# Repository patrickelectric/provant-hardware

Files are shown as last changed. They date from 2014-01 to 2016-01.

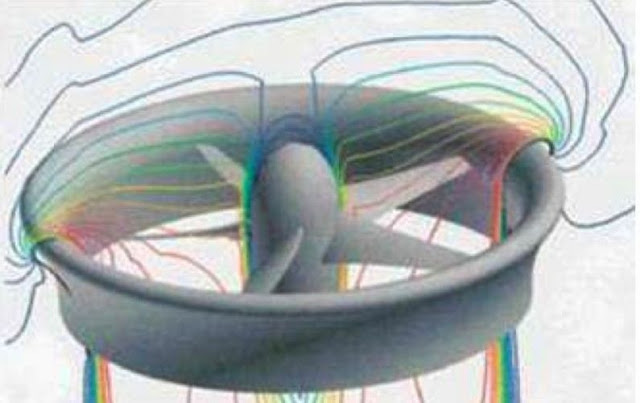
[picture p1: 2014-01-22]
mechanics/images/smCFDAeroAnal.jpg

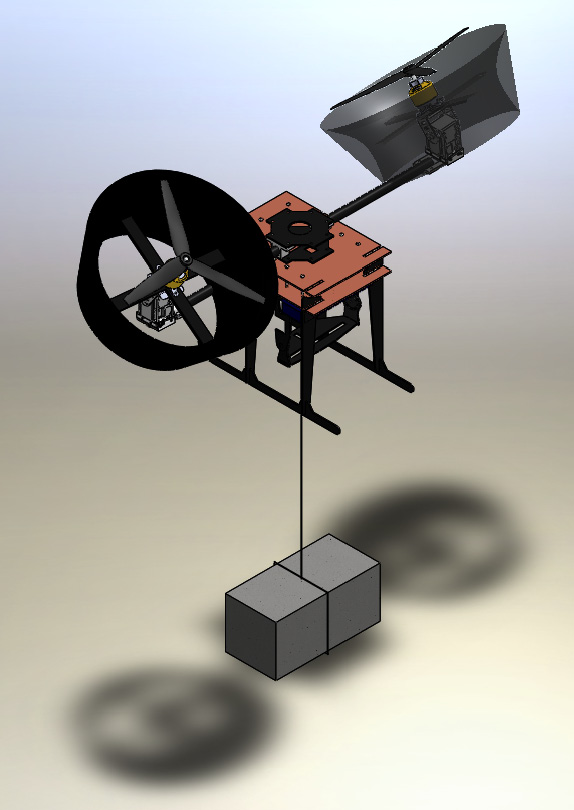
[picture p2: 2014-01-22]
mechanics/images/montagem_completa_tijolo_rodrigo.jpg

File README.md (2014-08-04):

provant-hardware
================

#### Descrição ####

Repositório para projeto de Hardware (mecânica e eletrônica) do proVANT. 

#### Estrutura do repositório ####

A pasta _mechanics_ está estruturada em três subpastas:

- __drawings__ : Desenhos técnicos das partes modeladas.
- __images__ :  Renderizações e _prints_ de modelos completos e peças. 
- __models__ : Arquivos dos modelos 3D de partes e montagens.

Os modelos 3D foram desenvolvidos em sua maioria com o uso do CAD [_Solid Works_](www.solidworks.com).

Os esquemáticos e layouts das placas deste projeto foram desenvolvidas com software de EDA [_Eagle_](www.cadsoftusa.com/), e estão contidos na pasta _electronics_. Esta está estruturada em:

- __lib__ :  Contem bibliotecas de componentes exclusivos do projeto, bem como bibliotecas de terceiros (não padrões no Eagle) que foram utilizadas.
- __stm32-e407-shield__ : Contem esquemático/layout do shield desenvolvido para a placa __antiga__ utilizada no projeto, a [STM32-H407](https://www.olimex.com/Products/ARM/ST/STM32-H407/open-source-hardware). Esta pasta e seus conteúdos podem ser considerados __obsoletos__ .
- __stm32f4discovery-shield__ : Contem o esquemático/layout da placa breakout sendo utilizada atualmente no projeto, projetada para a [STM32F4-Discovery](http://www.st.com/web/catalog/tools/FM116/SC959/SS1532/PF252419?sc=internet/evalboard/product/252419.jsp).

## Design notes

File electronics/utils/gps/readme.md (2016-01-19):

Manual de montagem dos perifericos do GPS
====================================

Todos os esquematicos nesta pasta foram realizados utilizando o Eagle, boa parte das bibliotecas utilizadas foram extraidas da [bilbioteca da SparkFun](https://github.com/sparkfun/SparkFun-Eagle-Libraries). 

##### Instalacao de bilbiotecas para o Eagle

O procedimento de instalacao das bibliotecas para o Eagle consta [neste link](
https://learn.sparkfun.com/tutorials/how-to-install-and-setup-eagle/using-the-sparkfun-libraries).

##### Connector_cable
Nesta pasta se encontra o conector utilizado para ter acesso aos pinos para leitura de dados basicos do GPS OEMStar, sendo eles: RX,TX,VCC,GND.

##### Connector_protoboard
Nesta pasta se encontra o conector utilizado para adaptar o conector do GPS OEMStar a protoboard.

##### Arduino_mini

Esta pasta em questao consta o conversor das mensagens do GPS para o VANT.
As mensagens que sao enviadas em formato de String sao de dificil tratamento utilizando as bibliotecas basicas do ARM que estao sendo atualmente utizadas no projeto.
Podendo variar o tamanho, formato e tipo.
As informacoes sobre as mensagens e o GPS podem ser encontradas [aqui](http://www.novatel.com/assets/Documents/Bulletins/apn026.pdf).

Alguns exemplos de mensagens recebidas:
```
#BESTPOSA,COM1,0,93.0,UNKNOWN,0,90.000,004c0000,7145,12014;INSUFFICIENT_OBS,NONE,0.00000000000,0.00000000000,0.0000,0.0000,WGS84,0.0000,0.0000,0.0000,"",0.000,0.000,0,0,0,0,0,00,00,00*18de8d75
#BESTPOSA,COM1,0,91.5,COARSESTEERING,1847,221137.000,004c0000,7145,12014;INSUFFICIENT_OBS,NONE,0.00000000000,0.00000000000,0.0000,0.0000,WGS84,0.0000,0.0000,0.0000,"",0.000,0.000,0,0,0,0,0,00,00,00*43baf10b
#BESTPOSA,COM1,0,87.0,FINESTEERING,1847,221347.000,00440000,7145,12014;SOL_COMPUTED,SINGLE,-27.60022826035,-48.51710556420,-2.9004,0.4000,WGS84,22.9611,14.4112,31.3712,"",0.000,0.000,4,4,4,4,0
```

#### Sobre o GPS
Boa parte da documentacao do GPS OEMStar pode ser encontrado dentro do Dropbox do projeto.
> proVANT/birotor/components/electronics/datasheets/sensors/GPS/novatek_oemstar

As bibliotecas para realizar a comunicação do GPS com o VANT esta localizado em:
> provant-software/io-board/stm32f4/base/modules/io/c_io_novatel.c/h

##### Iniciando comunicacao
Primeiramente deve ser feito um dos conectores, podendo ser tanto o connector_protoboard quanto o connector_cable, pois ambos dao acesso aos pinos basicos ditos anteriormente.

Os pinos que deveram ser conectados sao: 1,2 como VCC; 10,13,16,18 como GND; 11 como TX; 12 como RX;

| Signal | Behavior | Descriptions | Pin |
|---|---|---|-----|
| LNA_PWR  | Input DC | Power supply for external antenna | 1 |
| Vin | Input DC | DC power supply for card | 2 |
| USB d- | Bi-derectional | USB interface data - | 3 |
| USB d+ | Bi-directional | USB interface data + | 4 |
| RESETIN  | See strobes | Card reset | 5 |
| VARF | output | VARF | 6 |
| Reserved | | | |
| Reserved | | | |
| Event1 | Input | Strobe, see strobes, default: Event1 | 9 |
| GND | Ground | Digita Ground | 10  |
| COM1_Tx  | Output | Transmitted Data for COM 1 output | 11  |
| COM1_Rx  | Input | Receved Data for COM 1 input | 12  |
| GND | Ground | Digital Ground | 13  |
| COM2_Tx  | Output | Transmitted Data for COM 2 output | 14  |
| COM2_Rx  | Input | Received Data for COM 2 input | 15  |
| GND | Ground | Digital Ground | 16  |
| PV | Output | Output indicates 'good solution' or vallid FPS position when high | 17  |
| GND | Ground | Digital Gorund | 18  |
| PPS | See strobes | Pulse output synchronized to GPS Time | 19  |
| | | | |

Com estes pinos conectados em seus respectivos lugares, pode ser realizado os testes.

###### Software
Com os pinos conectados em um microcontrolador ou numa interface USB-serial, pode-se iniciar a comunicacao, com o baudrate de 9600, pedindo ao dispostivo a melhor posicao utilizando o comando:
```
LOG COM1 BESTPOSA ONTIME 1
```
Enquanto o GPS nao detectar a posicao, ele retornada a msg:
```
#BESTPOSA,COM1,0,93.0,UNKNOWN,0,90.000,004c0000,7145,12014;INSUFFICIENT_OBS,NONE,0.00000000000,0.00000000000,0.0000,0.0000,WGS84,0.0000,0.0000,0.0000,"",0.000,0.000,0,0,0,0,0,00,00,00*18de8d75
```

Um exemplo de codigo para ter uma comunicacao do GPS pode ser encontrado abaixo, este mesmo codigo pode ser utilizado para realizar a comunicacao do GPS com o VANT.
Este codigo foi utilizado para a placa arduino_mini, utilizando os pinos 10 e 11 para a comunicacao serial via software.

```
// all the information about the data can be obtained from: http://www.novatel.com/assets/Documents/Bulletins/apn026.pdf
// or on Dropbox: Geodetic Principles.pdf

// to start, send the command:
// log com1 bestposa ontime 1

#include <SoftwareSerial.h>

char * floatToString(char * outstr, float value, int places);

const int led = 13;
String started="[COM1]";
String bestposa="#BESTPOSA";
String unknown="UNKNOWN";
String coarsesteering="COARSESTEERING";
String finesteering="FINESTEERING";
String insufficient_obs="INSUFFICIENT_OBS";
String sol_computed="SOL_COMPUTED";

#define PROCESS_BESTPOSA      1
#define PROCESS_BESTPOSA_DATA 1
#define DEBUG                 1

//char  float_pos1[]={2,3}
//float Buffer[32]
bool SOL_COMPUTED_FLAG=0;
SoftwareSerial SoSerial(10, 11); // TX = digital pin 10, RX = digital pin 11

void setup() 
{
  delay(2000);
  // initialize serial:
  Serial.begin(9600);
  SoSerial.begin(9600);
  // make the pins outputs:
  pinMode(led, OUTPUT); 
}

void loop() 
{
  digitalWrite(led,HIGH);
  // if there's any serial available, read it:
  while (SoSerial.available() > 0)
  {
    digitalWrite(led,LOW);      // show that we received something
    char newlinearray[300]={};
    SoSerial.readBytesUntil('\n',newlinearray,300);
    String newline = newlinearray;
    
    if(DEBUG)
    {
      Serial.print("[R] >");
      Serial.print(newline);
      Serial.println("<");    // show what received
    }

    if(PROCESS_BESTPOSA && newline.length()>10)
    {
      // process bestposa
      int beginIdx = 0;
      int endIdx = newline.indexOf(";")-6;      // the last ',' of bestposa is ';' -6 char 
      int idx = newline.indexOf(",",beginIdx);  // take the first ','
      String arg[50];
      for(int i=0;i<50 && idx!=endIdx;i++)      // take all data
      {
        arg[i] = newline.substring(beginIdx, idx);
        beginIdx = idx + 1;
        idx = newline.indexOf(",", beginIdx);
        if(DEBUG)
        {
          Serial.print(i);
          Serial.print(" >");
          Serial.println(arg[i]);
        }
      }
    }

    if(DEBUG)
      Serial.println("###################");

    if(PROCESS_BESTPOSA_DATA && newline.length()>10)
    {
      // process data
      SOL_COMPUTED_FLAG = false;
      
      int beginIdx = newline.indexOf(";")+1;
      int endIdx = -1;
      int idx = newline.indexOf(",",beginIdx);
      String arg[50];
      
      for(int i=0;i<50 && idx!=endIdx;i++)
      {
        arg[i] = newline.substring(beginIdx, idx);
        beginIdx = idx + 1;
        idx = newline.indexOf(",", beginIdx);
        if(DEBUG)
        {
          Serial.print(i);
          Serial.print(" > ");
          Serial.println(arg[i]);
        }
      }
      if(arg[0] == sol_computed)
        SOL_COMPUTED_FLAG = true;

        if(SOL_COMPUTED_FLAG)
        {
          Serial.print("R");
          Serial.write(arg[2].length());
          Serial.write(arg[3].length());
          float heigh = arg[5].toFloat()+arg[4].toFloat();
          char buffer[25];
          String Heigh = floatToString(buffer, heigh, 5);
          Serial.write(Heigh.length());
          
          Serial.print(arg[2]);
          Serial.print(",");
          Serial.print(arg[3]);
          Serial.print(",");
          Serial.print(Heigh);
          
          Serial.print('\n');
        }
        else
        {
          Serial.print("R");
          Serial.write(13);
          Serial.write(13);
          Serial.write(7);
          Serial.print("0.00000000000");
          Serial.print(",");
          Serial.print("0.00000000000");
          Serial.print(",");
          Serial.print("0.00000");
          Serial.print('\n');
        }
    }   
    
  } // while serial avaiable

  // send data VANT->GPS
  while(Serial.available()>0)
  {
      SoSerial.write(Serial.read());
  }
      
}

char * floatToString(char * outstr, float value, int places)
{
   int minwidth=0;bool rightjustify=false;
    // this is used to write a float value to string, outstr.  oustr is also the return value.
    int digit;
    float tens = 0.1;
    int tenscount = 0;
    int i;
    float tempfloat = value;
    int c = 0;
    int charcount = 1;
    int extra = 0;
    // make sure we round properly. this could use pow from <math.h>, but doesn't seem worth the import
    // if this rounding step isn't here, the value  54.321 prints as 54.3209

    // calculate rounding term d:   0.5/pow(10,places)  
    float d = 0.5;
    if (value < 0)
        d *= -1.0;
    // divide by ten for each decimal place
    for (i = 0; i < places; i++)
        d/= 10.0;    
    // this small addition, combined with truncation will round our values properly 
    tempfloat +=  d;

    // first get value tens to be the large power of ten less than value    
    if (value < 0)
        tempfloat *= -1.0;
    while ((tens * 10.0) <= tempfloat) {
        tens *= 10.0;
        tenscount += 1;
    }

    if (tenscount > 0)
        charcount += tenscount;
    else
        charcount += 1;

    if (value < 0)
        charcount += 1;
    charcount += 1 + places;

    minwidth += 1; // both count the null final character
    if (minwidth > charcount){        
        extra = minwidth - charcount;
        charcount = minwidth;
    }

    if (extra > 0 and rightjustify) {
        for (int i = 0; i< extra; i++) {
            outstr[c++] = ' ';
        }
    }

    // write out the negative if needed
    if (value < 0)
        outstr[c++] = '-';

    if (tenscount == 0) 
        outstr[c++] = '0';

    for (i=0; i< tenscount; i++) {
        digit = (int) (tempfloat/tens);
        itoa(digit, &outstr[c++], 10);
        tempfloat = tempfloat - ((float)digit * tens);
        tens /= 10.0;
    }

    // if no places after decimal, stop now and return

    // otherwise, write the point and continue on
    if (places > 0)
    outstr[c++] = '.';

    // now write out each decimal place by shifting digits one by one into the ones place and writing the truncated value
    for (i = 0; i < places; i++) {
        tempfloat *= 10.0; 
        digit = (int) tempfloat;
        itoa(digit, &outstr[c++], 10);
        // once written, subtract off that digit
        tempfloat = tempfloat - (float) digit; 
    }
    if (extra > 0 and not rightjustify) {
        for (int i = 0; i< extra; i++) {
            outstr[c++] = ' ';
        }
    }

    outstr[c++] = '\0';
    return outstr;
}
```

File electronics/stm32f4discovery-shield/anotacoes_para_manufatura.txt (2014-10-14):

Anotações para schematic-for-manuf.brd
======================================

Tamanho de furações (mínimo do fabricante = 0.4mm)
+ Para conectores RJ11 - pads = 0.7mm [0,027559 polegadas]
+ Para conectores RJ11 - dois conectores mecânicos laterais = 2.0mm [0,078740 polegadas]
+ Para DIP (todas as barras de pino e de soquete) = 0.9mm [0,035433 polegadas]

Larguras de trilhas (mínimo do fabricante = 8mils)
+ Para malhas de sinais = 12 mil 
	(para passar trilhas entre pads é adequado. O espaço entre pads é de ~34mils; sobram ~11 mils pra cada lado, o que fica ok com o mínimo de espaçamento de 8mils do fabricante)
+ Para as malhas de alimentação = 24 mil (Linhas de 5V, 3V3 e GND se necessário). rip
+ para uma malha de alimentação, quando ela estiver conectando o último elemento de uma linha = 16mil

Tamanho dos pads: 
+ Pads e vias serao octogonais com 66mil de diametro. 

Diferenças principais entre a placa para fresagem e para manufatura
===================================================================

+ Parte-se do pressuposto de furos metalizados, que conectam o pad no TOP e no BOTTOM.
+ Utilizam-se trilhas partindo dos pads do TOP dos conectores RJ12 e no soquete da Discovery (barra-pino).
+ A tolerância apresentada na seção anterior permite o uso de trilhas passando por entre pads.

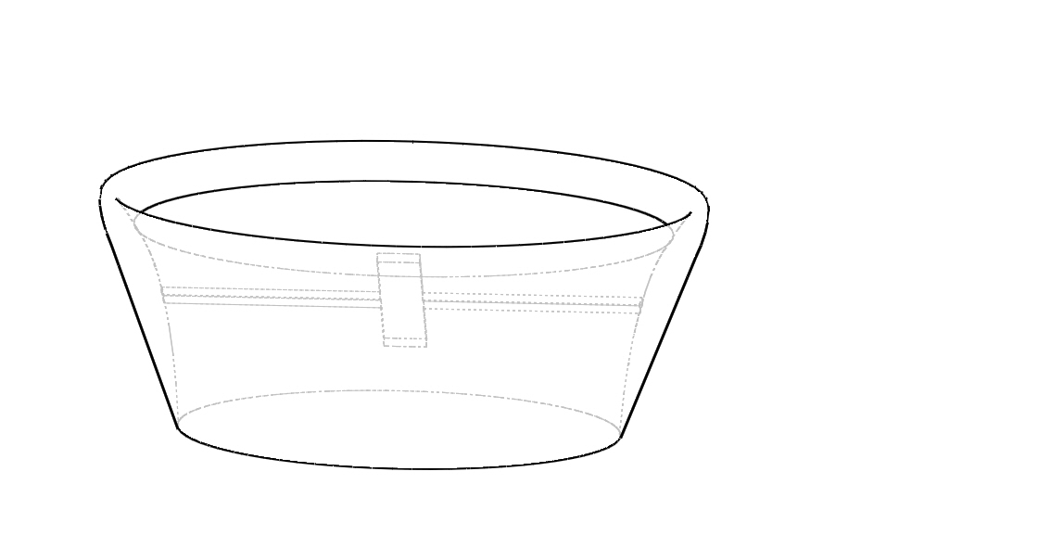
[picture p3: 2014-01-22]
mechanics/images/ducted fan_novo.JPG

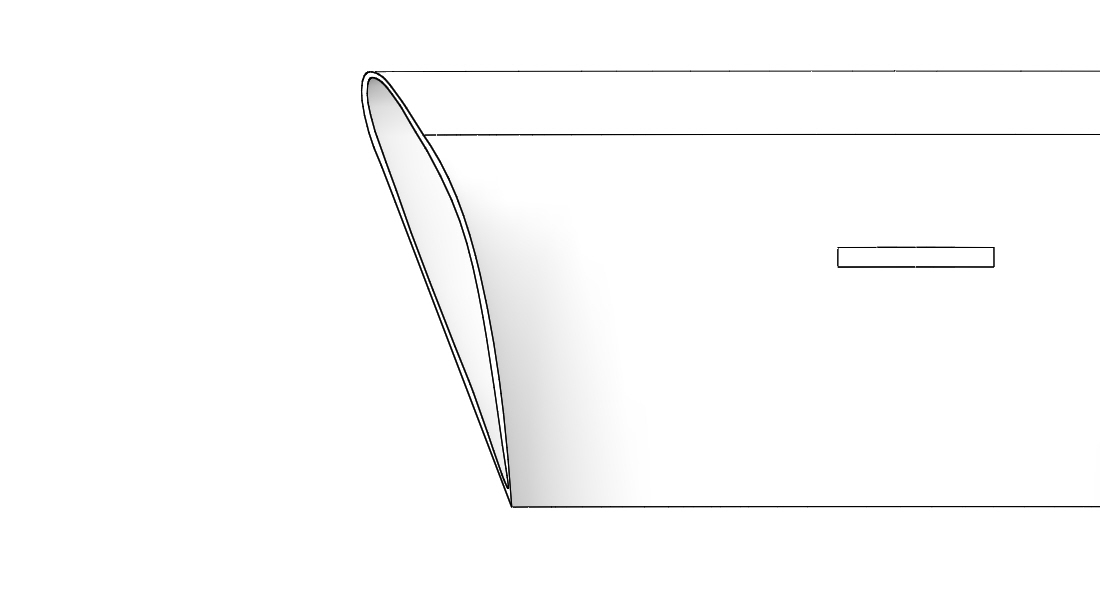
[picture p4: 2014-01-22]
mechanics/images/ducted fan_novo_corte.JPG

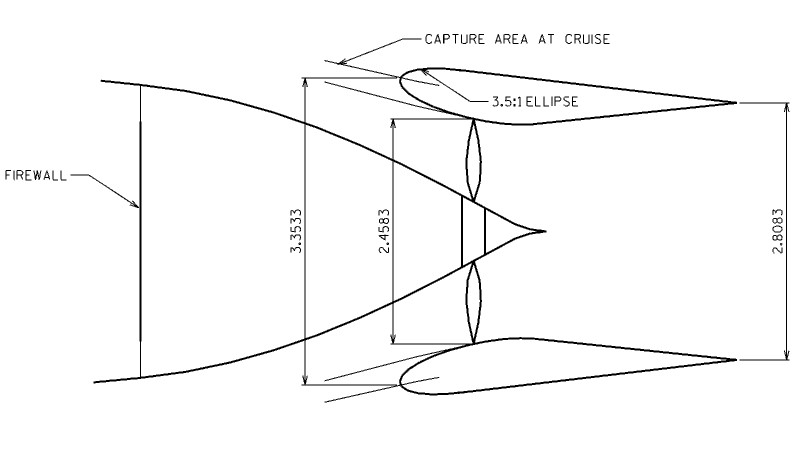
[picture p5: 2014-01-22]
mechanics/images/fanlayout.jpg

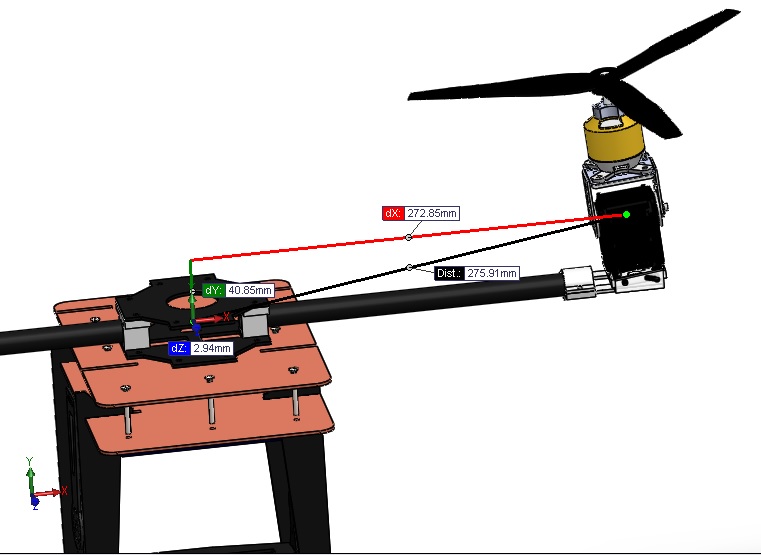
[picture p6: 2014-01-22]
mechanics/images/distancias_centro.jpg

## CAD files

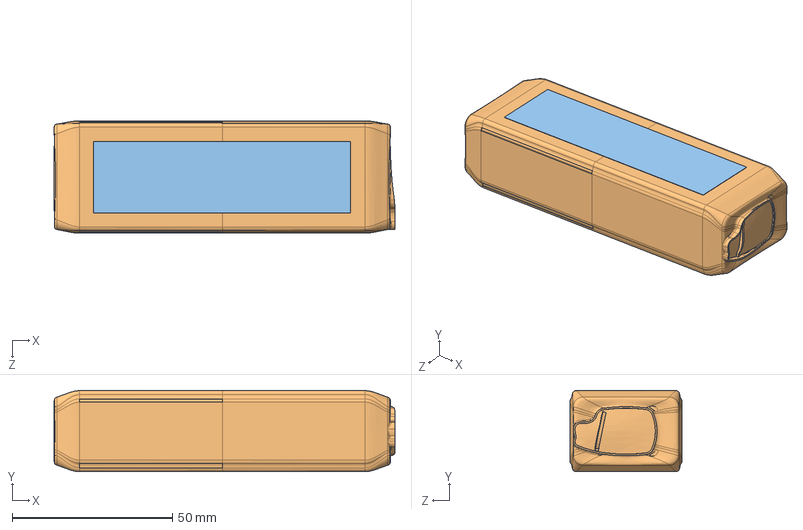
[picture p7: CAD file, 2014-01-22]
mechanics/models/Bateria/LiPo_1.SLDASM
106.3 x 25.4 x 35.0 mm
Inner end
Casing
Label

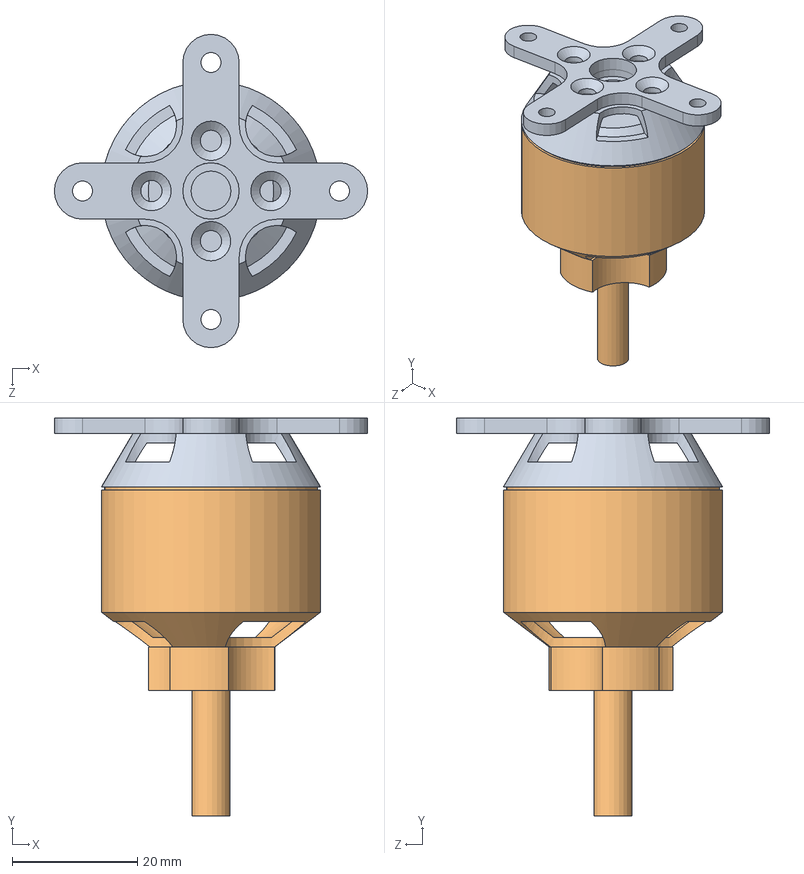
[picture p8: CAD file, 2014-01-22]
mechanics/models/MotorBrushless/MotorBrushless.SLDASM
50.0 x 63.5 x 50.0 mm
AXI2814-20-base
AXI2814-20-rotor^MotorBrushless

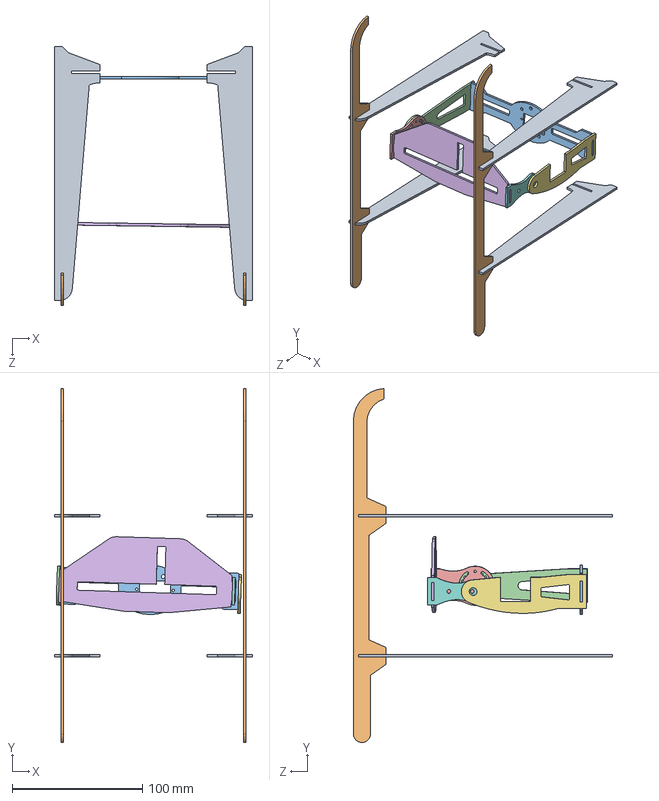
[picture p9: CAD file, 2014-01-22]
mechanics/models/trem_pouso_montagem.SLDASM
152.0 x 271.5 x 198.9 mm
tremdepouso_perna x 4
tremdepouso_sky x 2
Peça2
Peça5
Peça4
Peça3
Peça8-suporte_camera
Peça7-suporte_camera

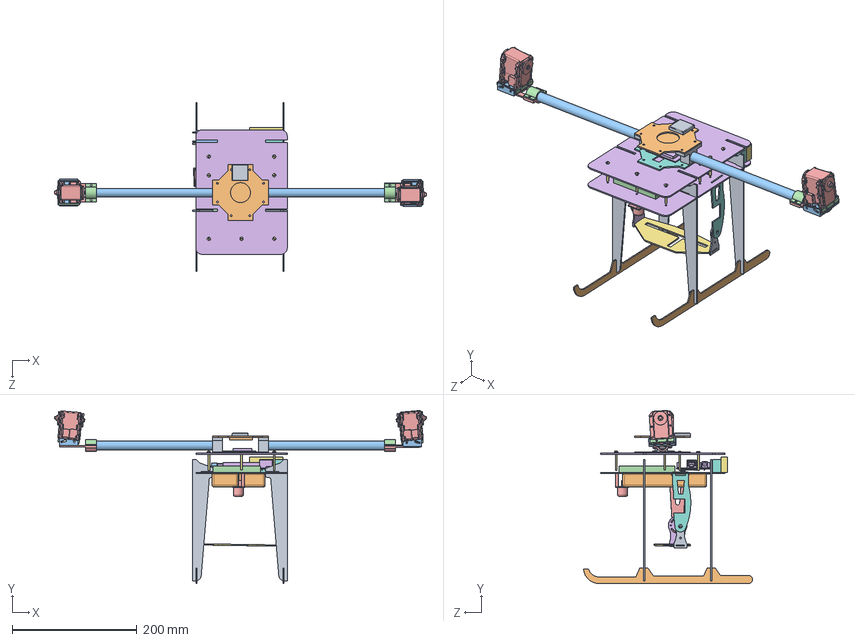
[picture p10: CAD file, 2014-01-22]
mechanics/models/montagem_inferior_eletronica.SLDASM
597.6 x 278.1 x 271.5 mm
tremdepouso_perna x 4
tremdepouso_sky x 2
Peça1
Peça2
Peça5
Peça4
Peça3
Peça8-suporte_camera
Peça7-suporte_camera
bateria1 x 2
suporte_inclinado_base x 2
suporte_inclinado_haste x 2
servo_rx24F x 2
chapa x 2
countersunk slotted raised head screw_iso x 9
centro_helice_2
suporte_haste x 2
centro_helice_1
helice_haste x 2
suporte_helice_2 x 2
suporte_helice x 2
Beagle
5v5a_converter
9v_45a_converter
gps_antenna
gps_base
rx
cortex m4
sonar
imu

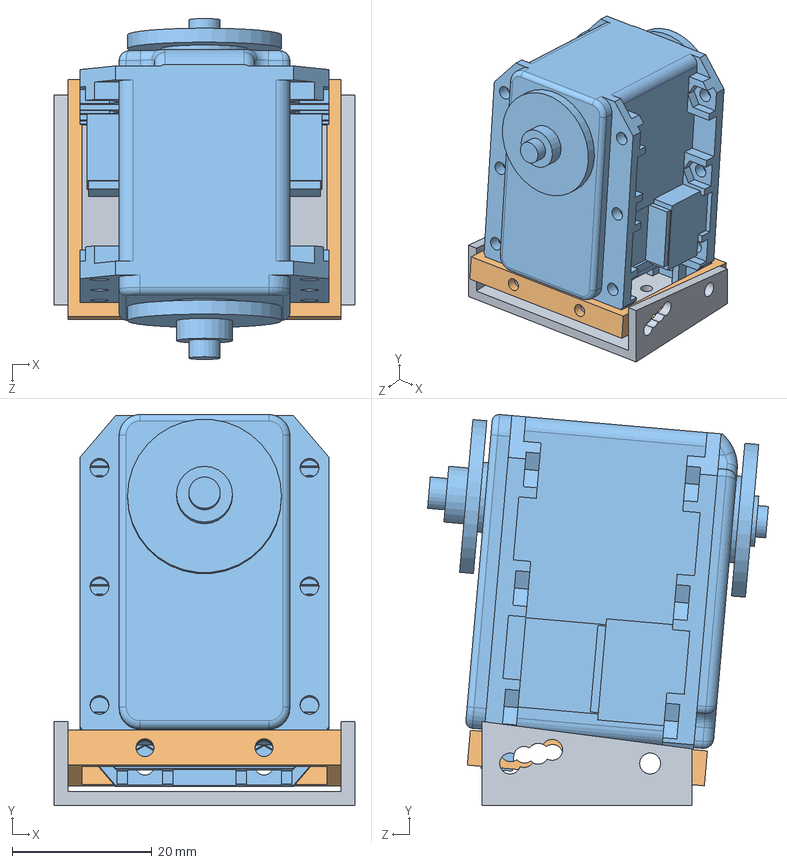
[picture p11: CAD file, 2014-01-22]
mechanics/models/suporte_inclinado_montagem_2.SLDASM
43.0 x 55.9 x 48.7 mm
suporte_inclinado_base
suporte_inclinado_haste
servo_rx24F

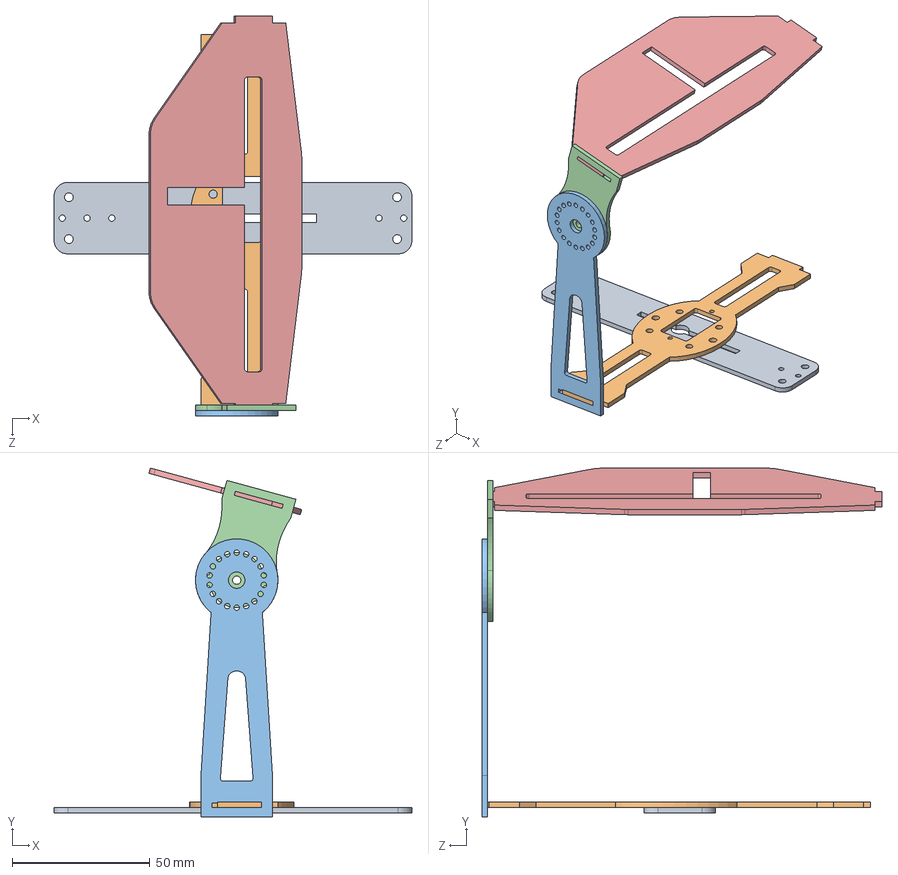
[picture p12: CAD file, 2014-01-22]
mechanics/models/suporte_camera.SLDASM
130.0 x 126.7 x 145.1 mm
Peça1
Peça2
Peça5
Peça4
Peça3

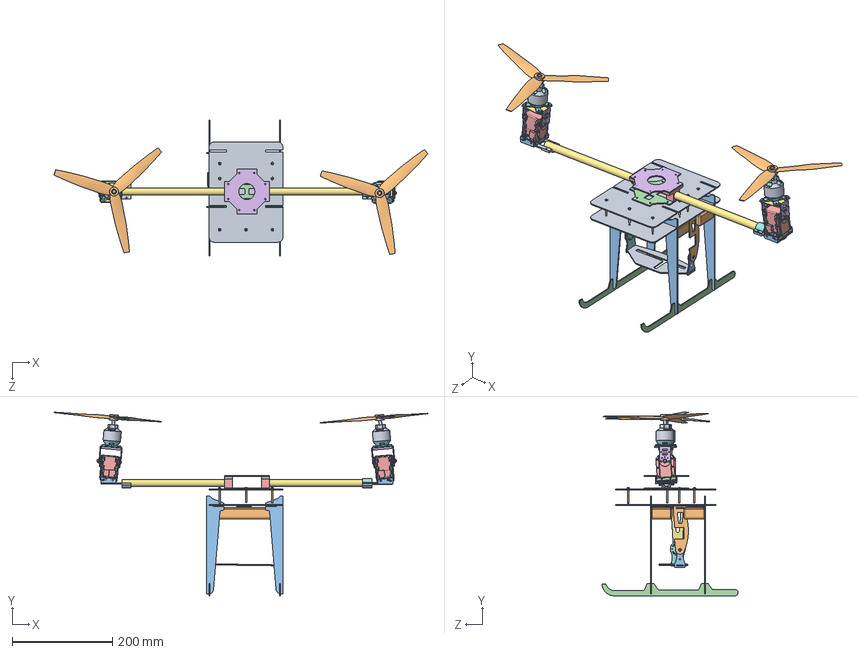
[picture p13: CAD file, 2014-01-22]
mechanics/models/montagem_completa.SLDASM
745.5 x 366.4 x 271.5 mm
chapa x 2
countersunk slotted raised head screw_iso x 9
tremdepouso_perna x 4
tremdepouso_sky x 2
Peça1
Peça2
Peça5
Peça4
Peça3
Peça8-suporte_camera
Peça7-suporte_camera
centro_helice_2
suporte_haste x 2
centro_helice_1
helice_haste x 2
suporte_helice_2
suporte_helice x 2
bateria1 x 2
suporte_inclinado_base x 2
suporte_inclinado_haste x 2
servo_rx24F x 2
motor_suporte_rotativo x 2
motor_chapa x 2
AXI2814-20-base x 2
AXI2814-20-rotor^AXI2814-20 x 2
helice x 2

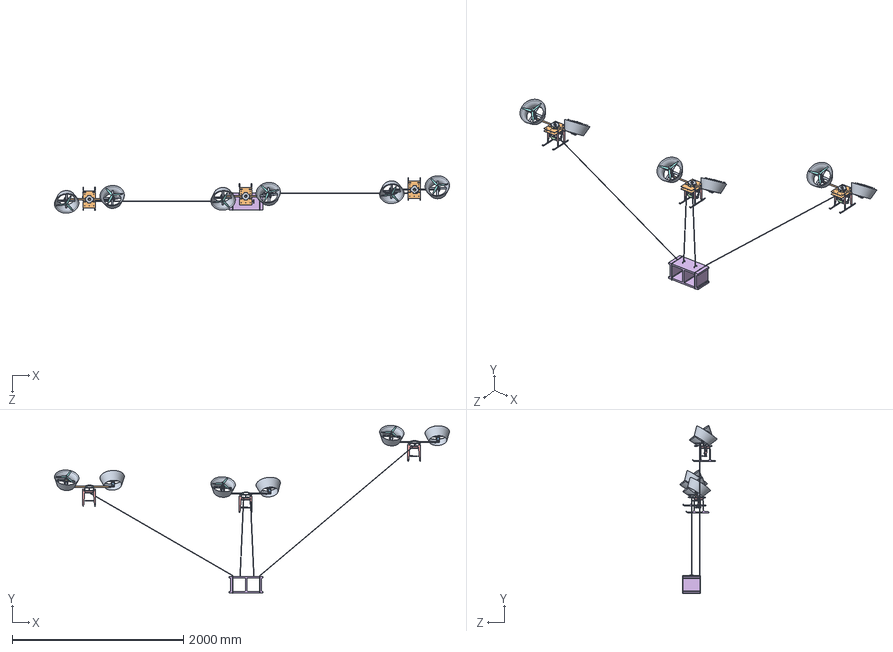
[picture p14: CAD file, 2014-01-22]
mechanics/models/montagem_completa_3.SLDASM
4613.3 x 1964.4 x 436.7 mm
suporte_inclinado_base x 6
suporte_inclinado_haste x 6
servo_rx24F x 6
motor_suporte_rotativo x 6
motor_chapa x 6
AXI2814-20-base x 6
AXI2814-20-rotor^AXI2814-20 x 6
helice x 6
ducted fan_novo x 6
chapa x 6
countersunk slotted raised head screw_iso x 27
tremdepouo_suporte_camera x 3
tremdepouso_perna x 12
tremdepouso_sky x 6
base_trem_pouso x 3
Peça1 x 3
Peça2 x 3
Peça5 x 3
Peça4 x 3
Peça3 x 3
Peça8-suporte_camera x 3
Peça7-suporte_camera x 3
centro_helice_2 x 3
suporte_haste x 6
centro_helice_1 x 3
helice_haste x 6
suporte_helice_2 x 3
suporte_helice x 6
bateria1 x 6
tijolo

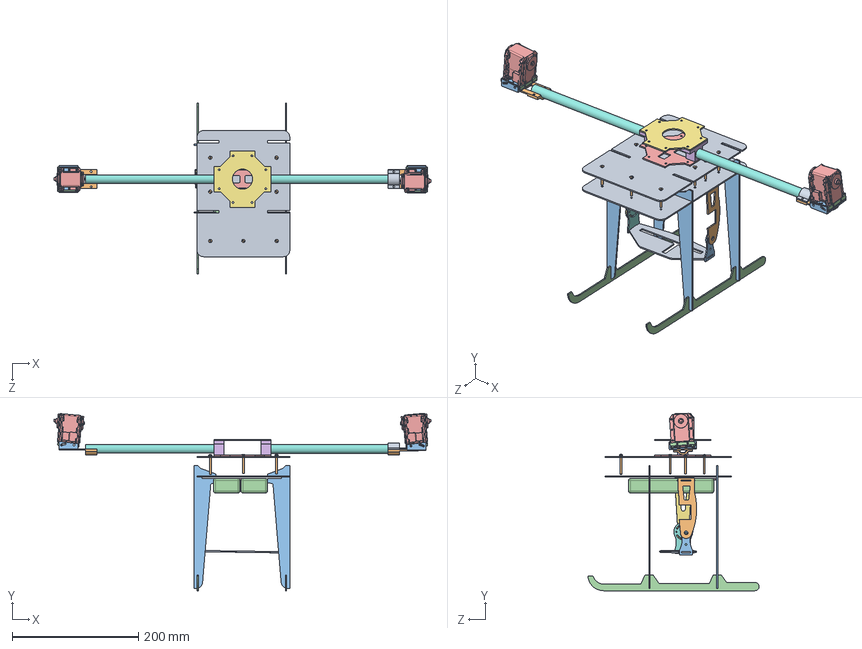
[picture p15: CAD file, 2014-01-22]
mechanics/models/montagem_inferior.SLDASM
597.6 x 281.4 x 271.5 mm
chapa x 2
countersunk slotted raised head screw_iso x 9
tremdepouso_perna x 4
tremdepouso_sky x 2
Peça1
Peça2
Peça5
Peça4
Peça3
Peça8-suporte_camera
Peça7-suporte_camera
bateria1 x 2
centro_helice_2
suporte_haste x 2
centro_helice_1
helice_haste x 2
suporte_helice_2
suporte_helice x 2
suporte_inclinado_base x 2
suporte_inclinado_haste x 2
servo_rx24F x 2

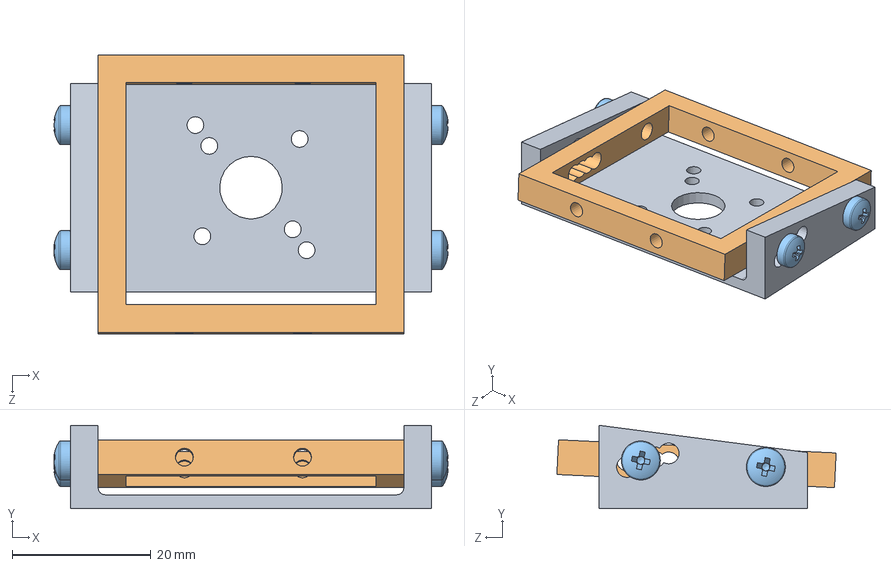
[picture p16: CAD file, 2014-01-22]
mechanics/models/montagemservo.SLDASM
56.7 x 12.0 x 40.2 mm
suporte_inclinado_base_2
suporte_inclinado_haste_2
pan head cross recess screw_iso x 4

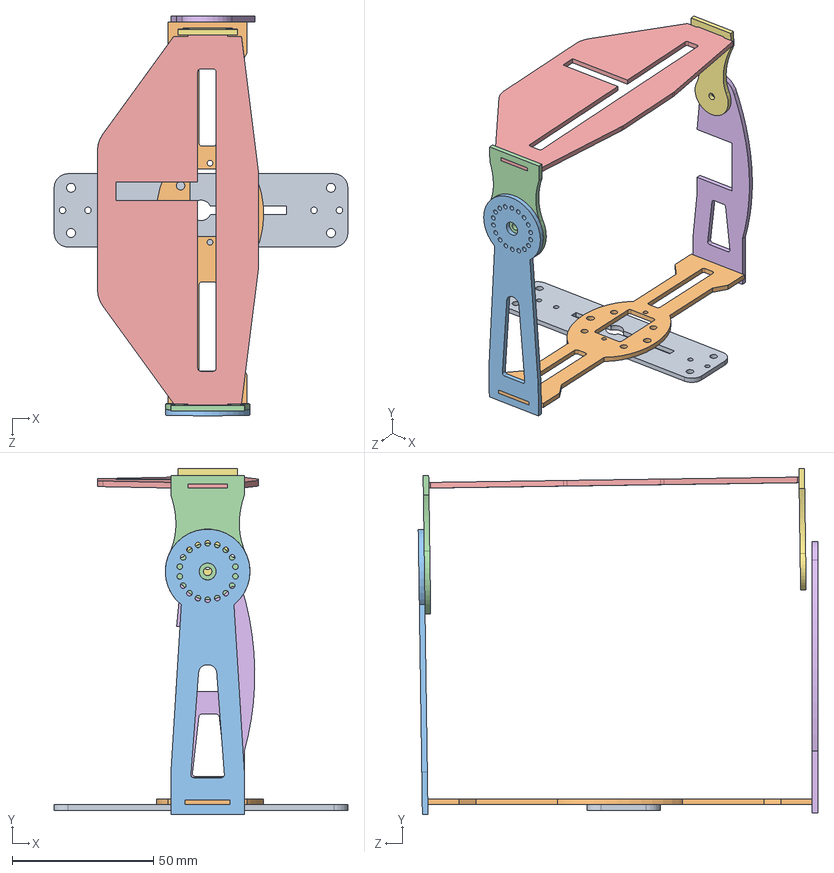
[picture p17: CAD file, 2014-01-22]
mechanics/models/suporte_camera_montagem.SLDASM
104.0 x 122.5 x 141.4 mm
Peça1
Peça2
Peça5
Peça4
Peça3
Peça8-suporte_camera
Peça7-suporte_camera

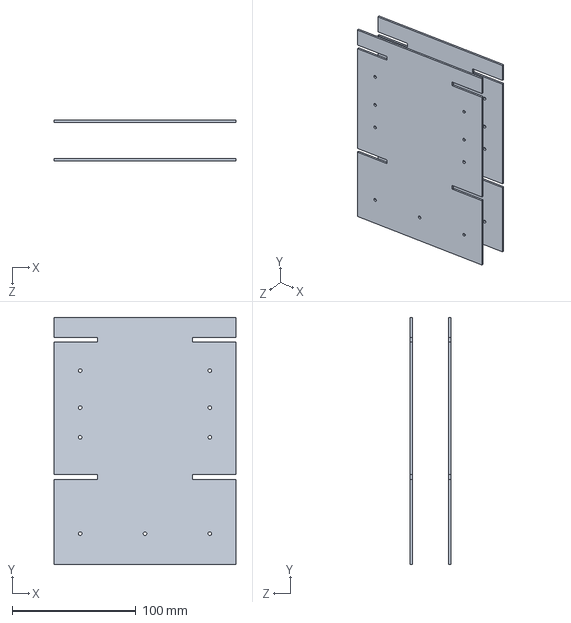
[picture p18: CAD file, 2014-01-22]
mechanics/models/chapa_montagem.SLDASM
147.0 x 200.0 x 33.0 mm
chapa x 2

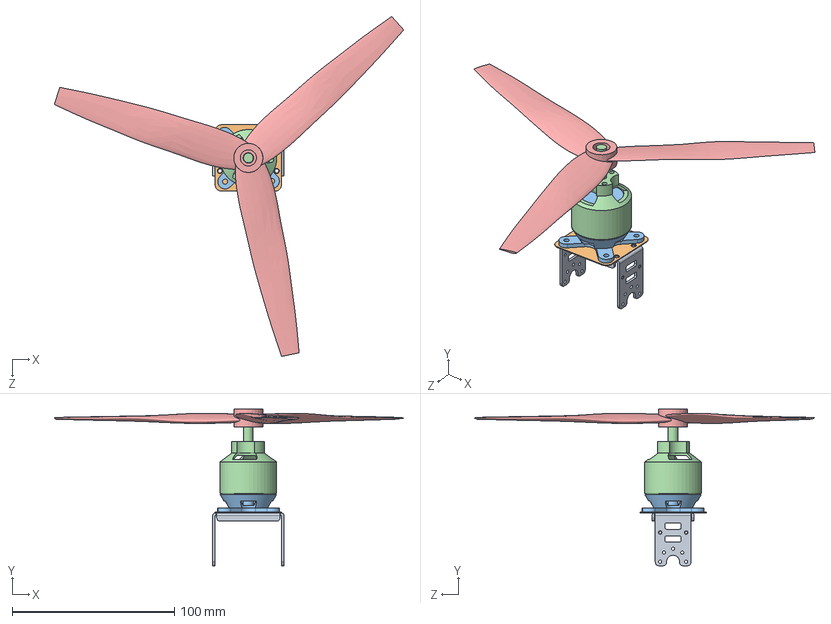
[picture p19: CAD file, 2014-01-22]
mechanics/models/montagem_superior.SLDASM
215.5 x 96.5 x 209.6 mm
motor_suporte_rotativo
motor_chapa
AXI2814-20-base
AXI2814-20-rotor^AXI2814-20
helice

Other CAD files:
mechanics/models/Bateria/Plug.sldasm
mechanics/models/Bateria/3-5mm Bullit Plug.sldasm
mechanics/models/Bateria/Batt.sldasm
mechanics/models/Bateria/EC3 Connector Assembly.sldasm
mechanics/models/motor.SLDASM
electronics/utils/gps/connector_cable/connector.dxf
mechanics/drawings/SW/centro_helice_1.SLDDRW
mechanics/drawings/SW/centro_helice_2.SLDDRW
mechanics/drawings/SW/desenhos.SLDDRW
mechanics/drawings/SW/ducted fan.SLDDRW
mechanics/drawings/SW/folha.SLDDRW
mechanics/drawings/SW/haste_helice.SLDDRW
mechanics/drawings/SW/helice.SLDDRW
mechanics/drawings/SW/suporte_camera_peça1.SLDDRW
mechanics/drawings/SW/suporte_camera_peça2.SLDDRW
mechanics/drawings/SW/suporte_camera_peça3.SLDDRW
mechanics/drawings/SW/suporte_camera_peça4.SLDDRW
mechanics/drawings/SW/suporte_camera_peça5.SLDDRW
mechanics/drawings/SW/suporte_camera_peça6.SLDDRW
mechanics/drawings/SW/suporte_camera_peça7.SLDDRW
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

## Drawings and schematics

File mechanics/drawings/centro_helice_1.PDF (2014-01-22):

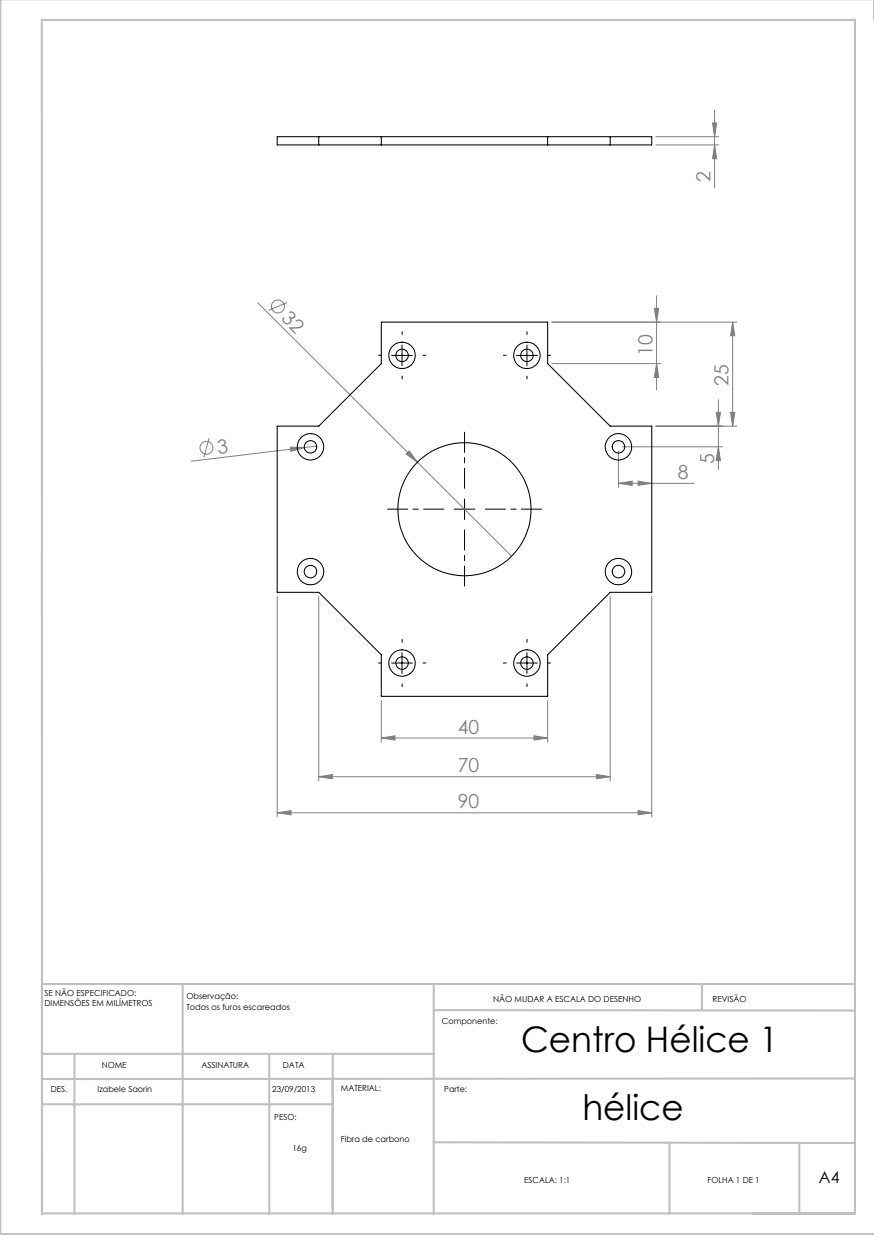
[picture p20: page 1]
NÃO MUDAR A ESCALA DO DESENHO; REVISÃO; Centro Hélice 1

SE NÃO ESPECIFICADO:
DIMENSÕES EM MILÍMETROS

Observação:
Todos os furos escareados

NOME | ASSINATURA | DATA

DES. | | | 23/09/2013 | MATERIAL: Fibra de carbono | Parte: hélice Izabele Saorin

PESO: 16g

ESCALA: 1:1 | FOLHA 1 DE 1 | A4

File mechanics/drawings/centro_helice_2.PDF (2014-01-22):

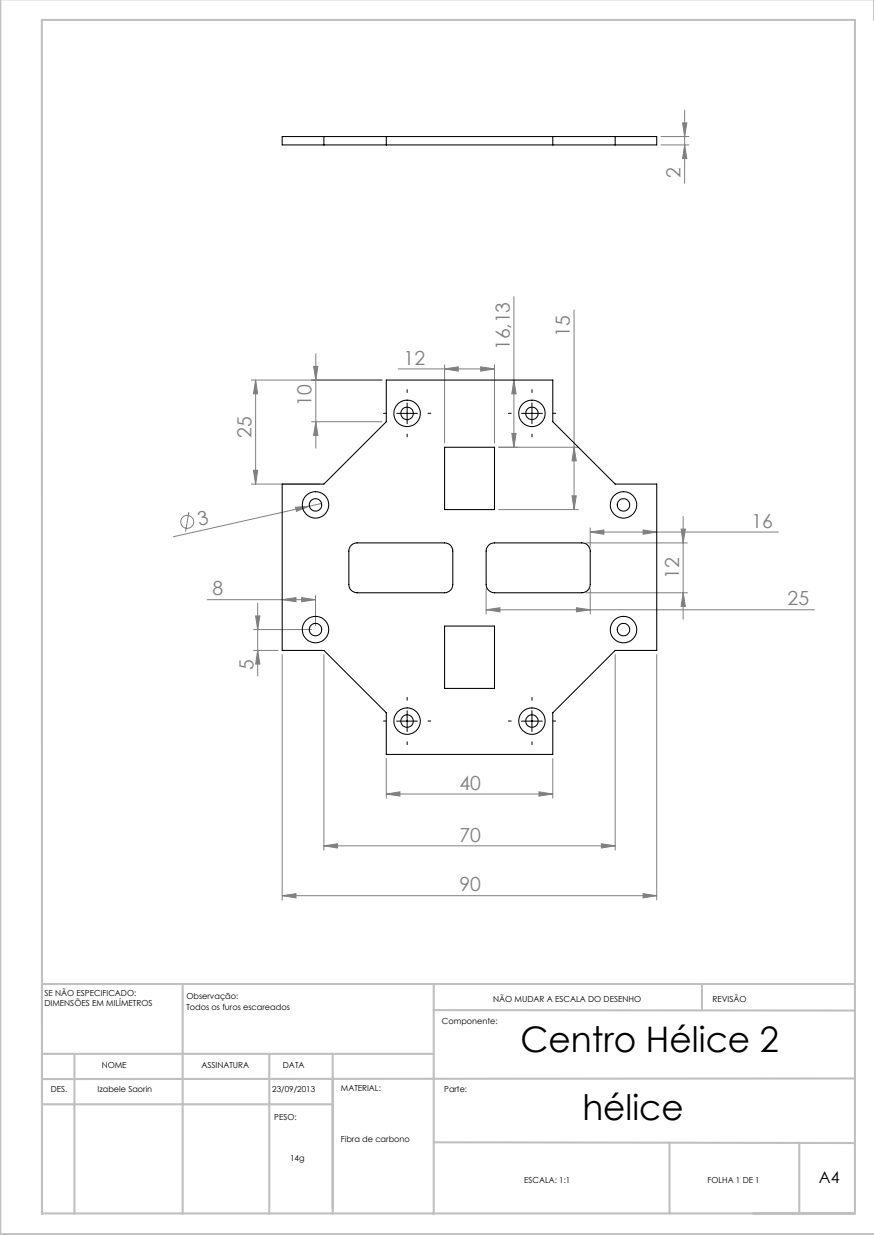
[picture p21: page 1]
NÃO MUDAR A ESCALA DO DESENHO; REVISÃO; Centro Hélice 2

SE NÃO ESPECIFICADO:
DIMENSÕES EM MILÍMETROS

Observação:
Todos os furos escareados

NOME | ASSINATURA | DATA

DES. | | | 23/09/2013 | MATERIAL: Fibra de carbono | Parte: hélice Izabele Saorin

PESO: 14g

ESCALA: 1:1 | FOLHA 1 DE 1 | A4

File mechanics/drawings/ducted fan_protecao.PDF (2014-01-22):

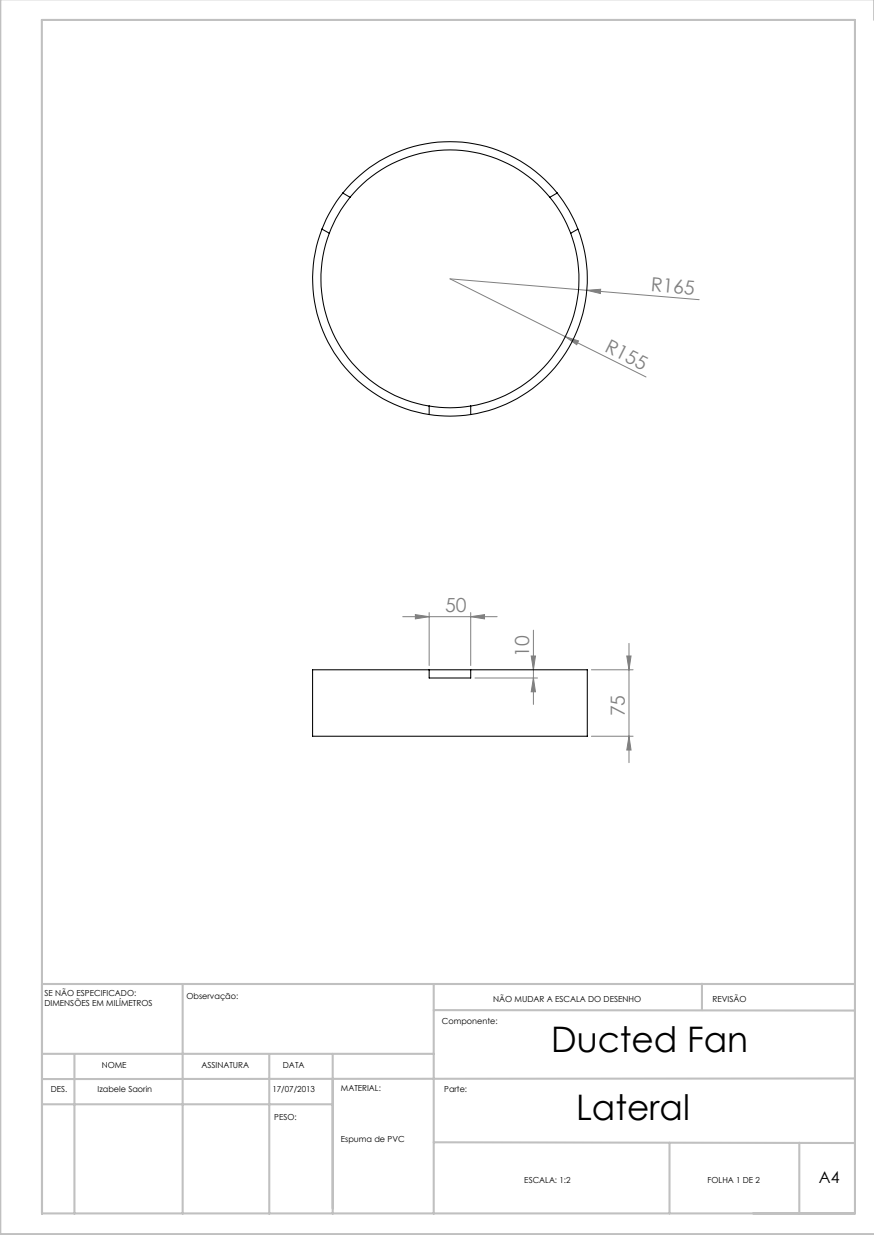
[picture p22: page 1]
NÃO MUDAR A ESCALA DO DESENHO; REVISÃO; Ducted Fan

Observação: SE NÃO ESPECIFICADO:
DIMENSÕES EM MILÍMETROS

NOME | ASSINATURA | DATA

DES. | | | 17/07/2013 | MATERIAL: Espuma de PVC | Parte: Lateral Izabele Saorin

PESO:

ESCALA: 1:2 | FOLHA 1 DE 2 | A4

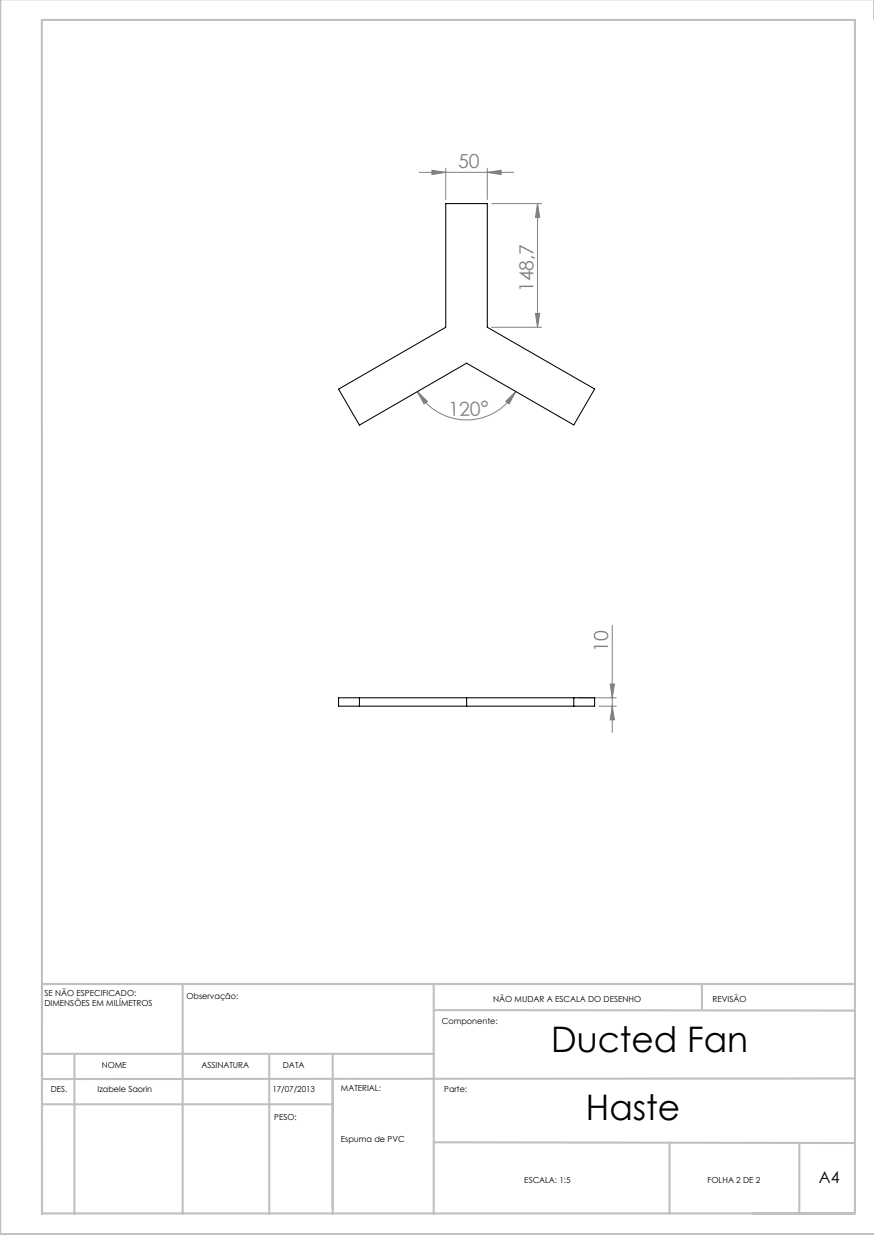
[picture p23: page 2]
NÃO MUDAR A ESCALA DO DESENHO; REVISÃO; Ducted Fan

Observação: SE NÃO ESPECIFICADO:
DIMENSÕES EM MILÍMETROS

NOME | ASSINATURA | DATA

DES. | | | 17/07/2013 | MATERIAL: Espuma de PVC | Parte: Haste Izabele Saorin

PESO:

ESCALA: 1:5 | FOLHA 2 DE 2 | A4

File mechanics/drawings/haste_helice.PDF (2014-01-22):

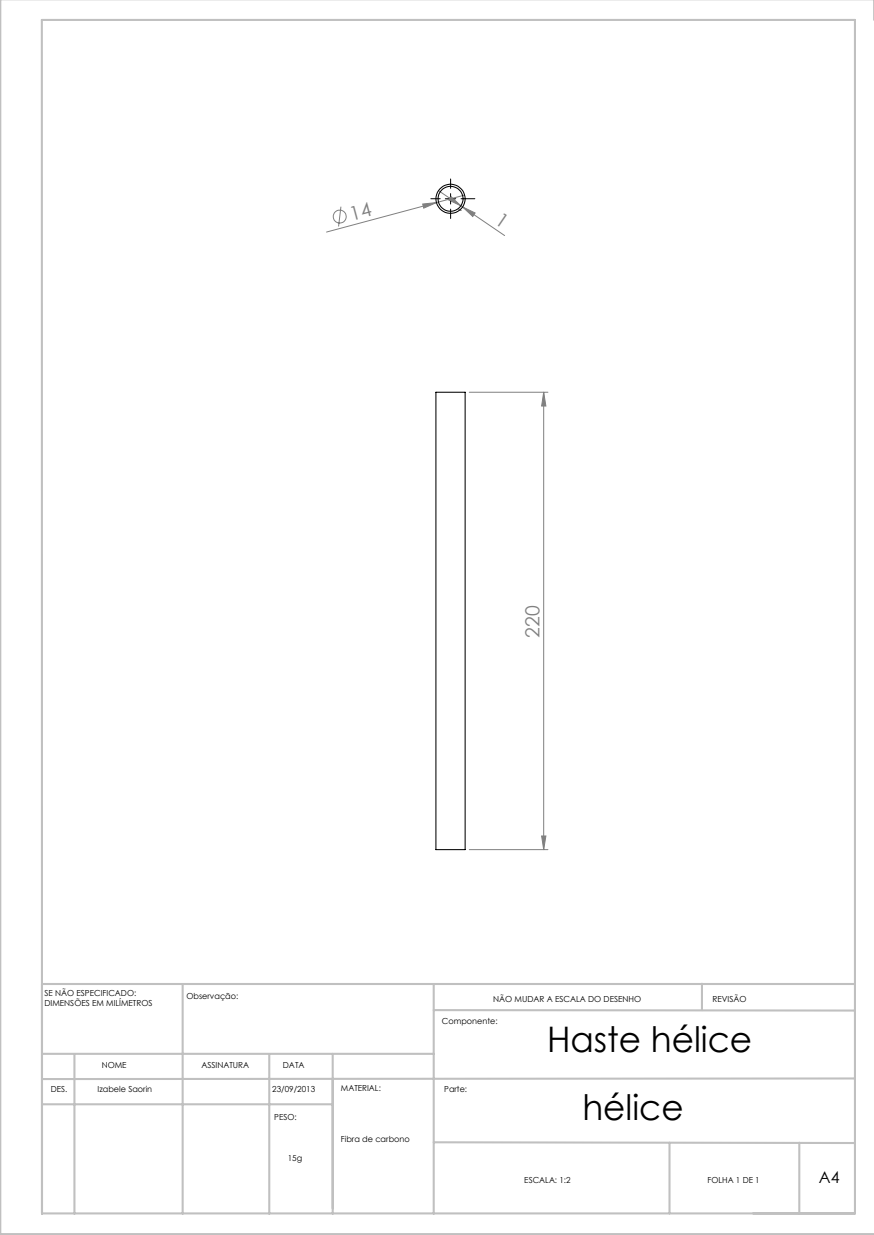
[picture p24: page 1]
NÃO MUDAR A ESCALA DO DESENHO; REVISÃO; Haste hélice

Observação: SE NÃO ESPECIFICADO:
DIMENSÕES EM MILÍMETROS

NOME | ASSINATURA | DATA

DES. | | | 23/09/2013 | MATERIAL: Fibra de carbono | Parte: hélice Izabele Saorin

PESO: 15g

ESCALA: 1:2 | FOLHA 1 DE 1 | A4

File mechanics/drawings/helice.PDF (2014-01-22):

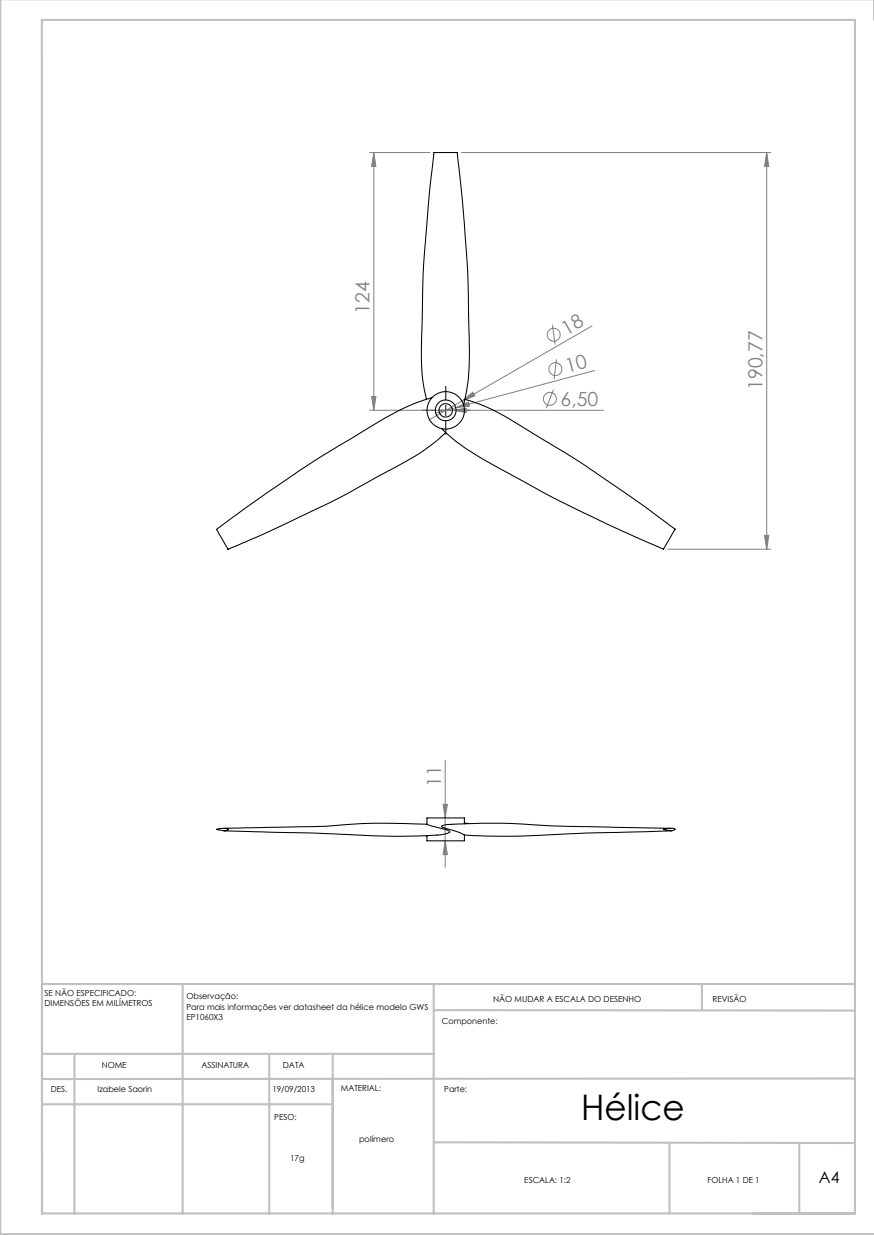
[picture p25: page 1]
NÃO MUDAR A ESCALA DO DESENHO; REVISÃO

SE NÃO ESPECIFICADO:
DIMENSÕES EM MILÍMETROS

Observação:
Para mais informações ver datasheet da hélice modelo GWS

NOME | ASSINATURA | DATA

DES. | | | 19/09/2013 | MATERIAL: polímero | Parte: Hélice Izabele Saorin

PESO: 17g

ESCALA: 1:2 | FOLHA 1 DE 1 | A4

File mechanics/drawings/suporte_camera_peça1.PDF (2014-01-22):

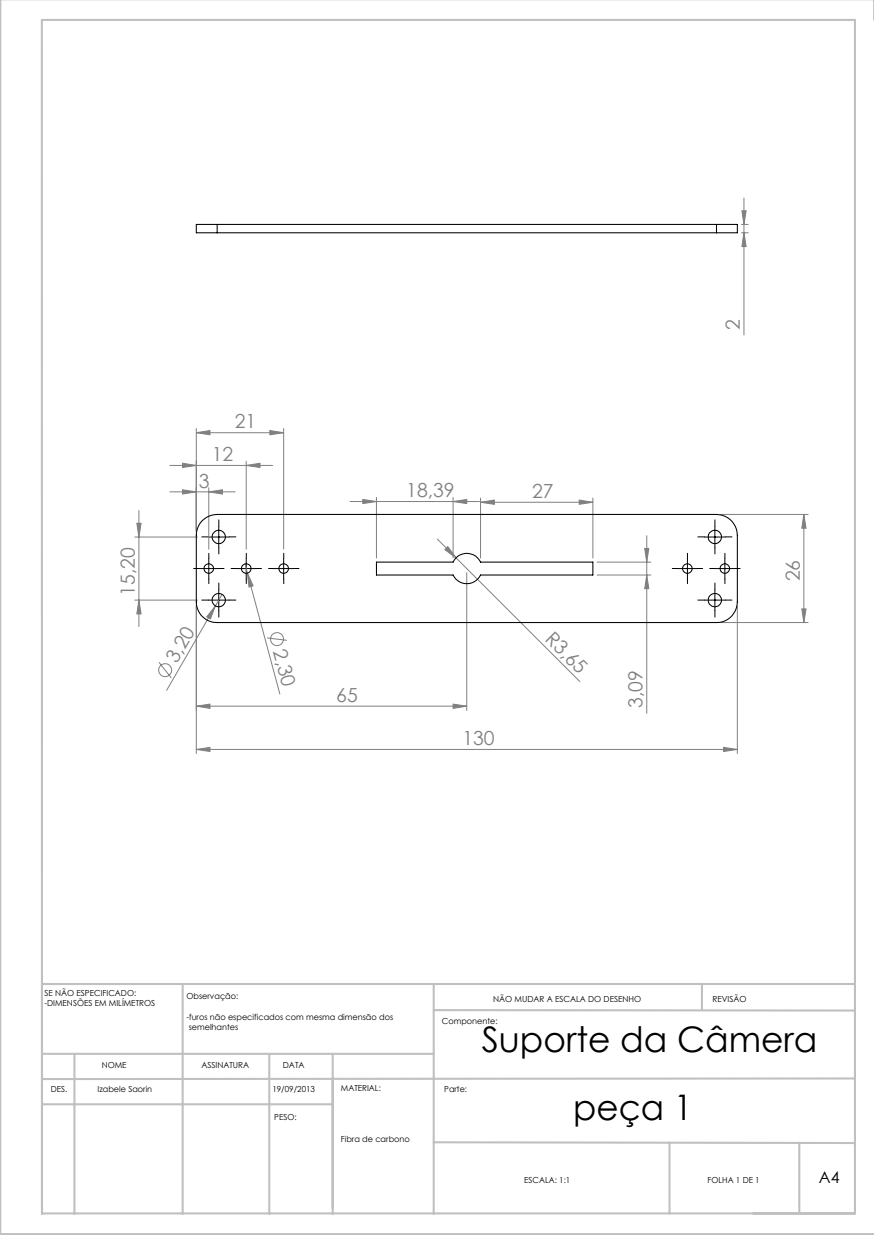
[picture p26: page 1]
NÃO MUDAR A ESCALA DO DESENHO; REVISÃO

SE NÃO ESPECIFICADO:
-DIMENSÕES EM MILÍMETROS

Observação:
-furos não especificados com mesma dimensão dos
semelhantes

Suporte da Câmera

NOME | ASSINATURA | DATA

DES. | | | 19/09/2013 | MATERIAL: Fibra de carbono | Parte: peça 1 Izabele Saorin

PESO:

ESCALA: 1:1 | FOLHA 1 DE 1 | A4

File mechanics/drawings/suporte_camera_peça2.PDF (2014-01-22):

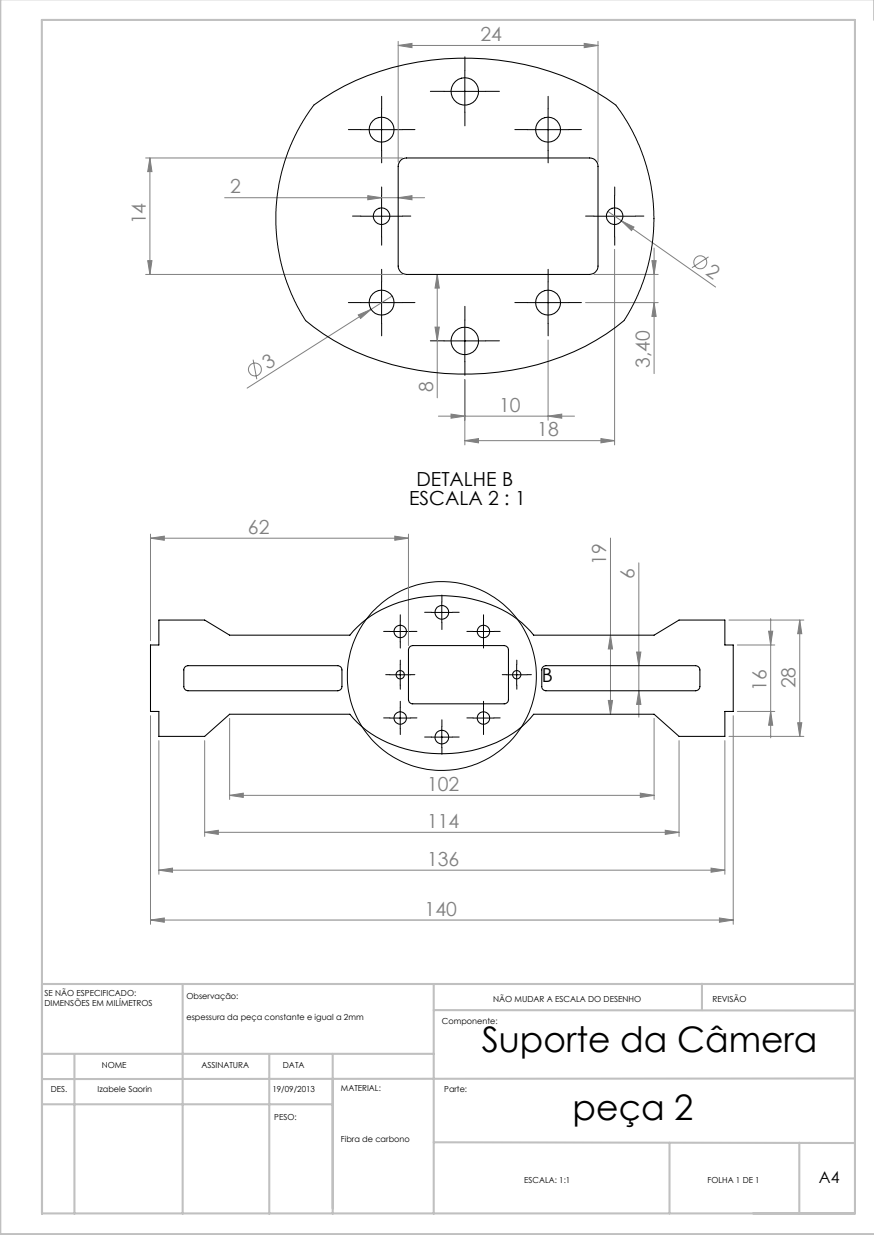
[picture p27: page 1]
DETALHE B ESCALA 2 : 1; NÃO MUDAR A ESCALA DO DESENHO; REVISÃO

SE NÃO ESPECIFICADO:
DIMENSÕES EM MILÍMETROS

Observação:
espessura da peça constante e igual a 2mm

Suporte da Câmera

NOME | ASSINATURA | DATA

DES. | | | 19/09/2013 | MATERIAL: Fibra de carbono | Parte: peça 2 Izabele Saorin

PESO:

ESCALA: 1:1 | FOLHA 1 DE 1 | A4

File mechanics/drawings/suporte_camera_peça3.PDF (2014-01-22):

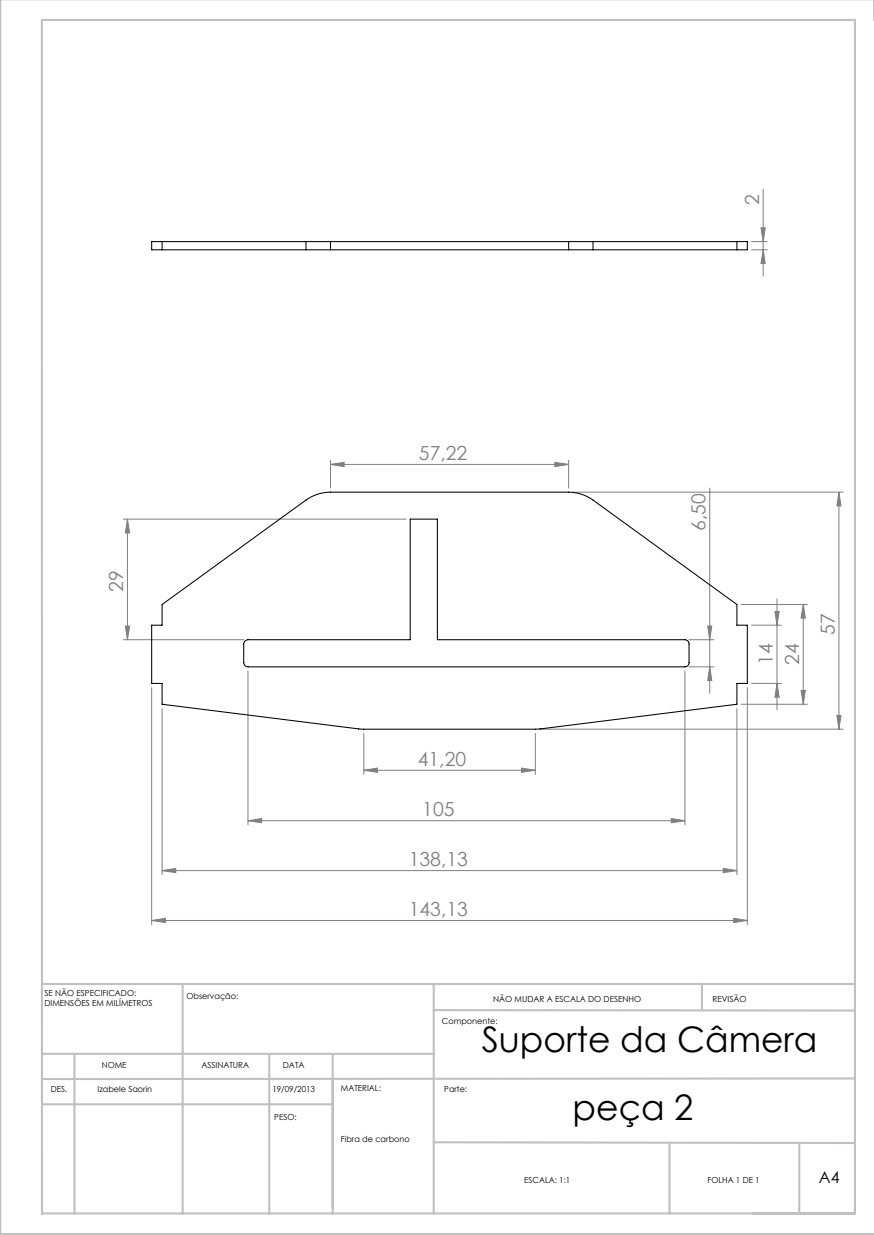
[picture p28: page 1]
NÃO MUDAR A ESCALA DO DESENHO; REVISÃO

Observação: SE NÃO ESPECIFICADO:
DIMENSÕES EM MILÍMETROS

Suporte da Câmera

NOME | ASSINATURA | DATA

DES. | | | 19/09/2013 | MATERIAL: Fibra de carbono | Parte: peça 2 Izabele Saorin

PESO:

ESCALA: 1:1 | FOLHA 1 DE 1 | A4

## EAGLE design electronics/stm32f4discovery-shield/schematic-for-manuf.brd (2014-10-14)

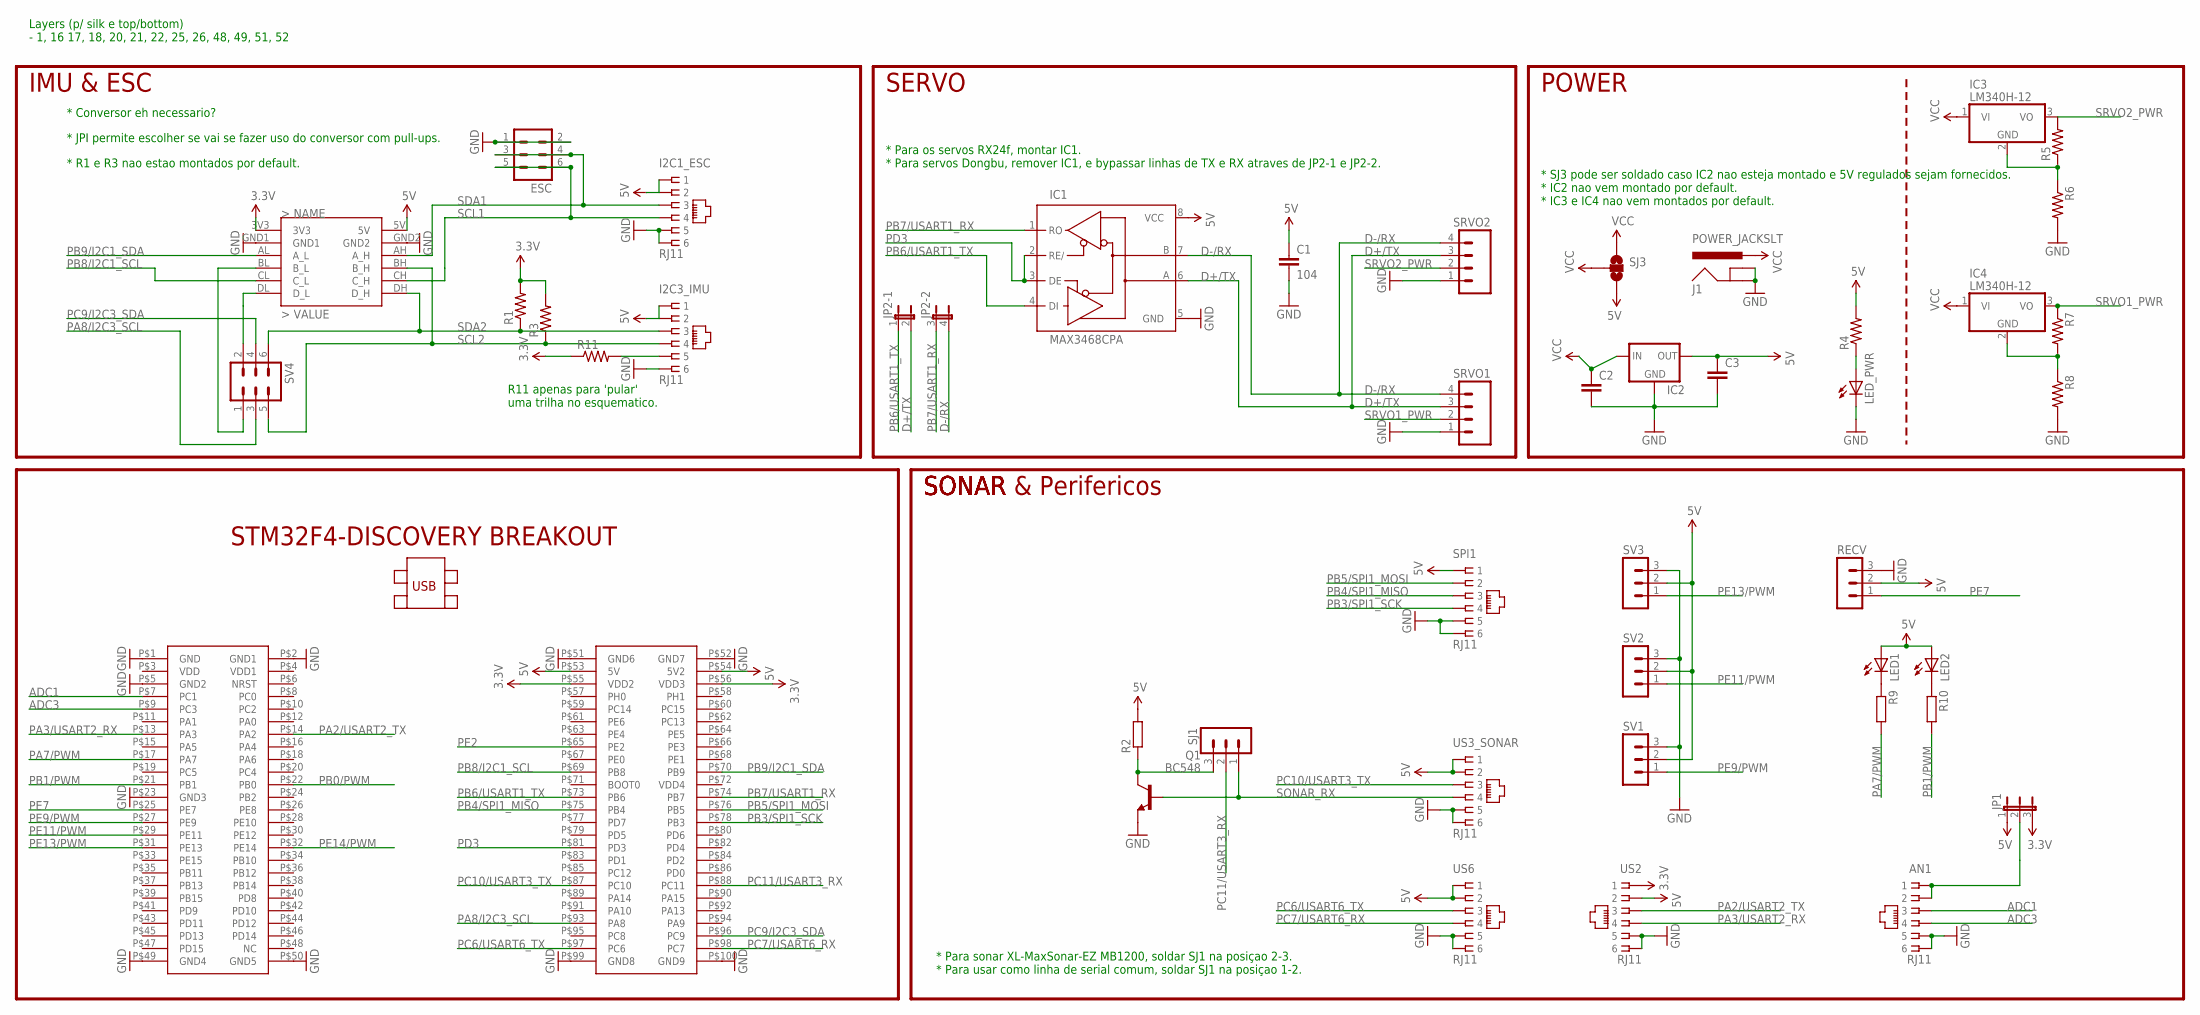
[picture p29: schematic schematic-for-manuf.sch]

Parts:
AN1: RJ11; RJ12-PROVANT
C1: 104; CAP-PTH-SMALL-KIT
C2: C7.5/3; C7.5B3
C3: 0.1UF-50V-20%(PTH)KIT-EZ; CAP-PTH-SMALL-KIT
ESC: MA03-2
I2C1_ESC, I2C3_IMU: RJ11; RJ12-PROVANT
IC1: MAX3468CPA; DIL08
IC2: V_REG_78XX-TO-220; TO-220-ALT
IC3, IC4: LM340H-12; TO220H
J1: POWER_JACKSLT; POWER_JACK_SLOT
JP1: JP2E; JP2
JP2: JP2QE; JP2Q
LED1, LED2: LED3MM
LED_PWR: LED5MM
Q1: BC548; TO92-EBC
R1, R3: R-US_0204/5; 0204/5
R2: R-EU_0204/7; 0204/7
R4, R5, R6, R7, R8: R-US_0204/7; 0204/7
R9, R10: R-EU_0204/2V; 0204V
R11: R-US_M1406; M1406
RECV: MA03-1
SJ1: MA03-1
SJ3: SOLDERJUMPER_2WAY-OLDW; SJ_2W
SPI1: RJ11; RJ12-PROVANT
SRVO1, SRVO2: M04POLAR; MOLEX-1X4
SV1, SV2, SV3: MA03-1
SV4: MA03-2
U$1: STM32F4-DISCOVERY
U$2: JYMCU_LOGIC_LEVEL_CONVERTER; JYMCU_LOGIC_LEVEL_SHIFTER_DIP
US2, US3_SONAR, US6: RJ11; RJ12-PROVANT

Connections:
3.3V: JP1.3, R1.2, R3.2, R11.1, U$1.P$55 (VDD2), U$1.P$56 (VDD3), U$2.3V3, US2.P1 (1)
5V: C1.1, C3.1, I2C1_ESC.P1 (1), I2C1_ESC.P2 (2), I2C3_IMU.P1 (1), I2C3_IMU.P2 (2), IC1.8 (VCC), IC2.OUT, JP1.1, LED1.A, LED2.A, R2.2, R4.2, RECV.2, SJ3.3, SPI1.P1 (1), SV1.2, SV2.2, SV3.2, U$1.P$53 (5V), U$1.P$54 (5V2), U$2.5V, US2.P2 (2), US3_SONAR.P1 (1), US3_SONAR.P2 (2), US6.P1 (1), US6.P2 (2)
ADC1: AN1.P3 (3), U$1.P$7 (PC1)
ADC3: AN1.P4 (4), U$1.P$9 (PC3)
D+/TX: IC1.6 (A), JP2.2, SRVO1.3, SRVO2.3
D-/RX: IC1.7 (B), JP2.4 (2), SRVO1.4, SRVO2.4
GND: AN1.P5 (5), AN1.P6 (6), C1.2, C2.2, C3.2, ESC.1, ESC.2, I2C1_ESC.P5 (5), I2C1_ESC.P6 (6), I2C3_IMU.P6 (6), IC1.5 (GND), IC2.GND, J1.GND@1 (GNDBREAK), J1.GND@2 (GND), LED_PWR.K (C), Q1.E, R6.2, R8.2, RECV.3, SPI1.P5 (5), SPI1.P6 (6), SRVO1.1, SRVO2.1, SV1.3, SV2.3, SV3.3, U$1.P$1 (GND), U$1.P$2 (GND1), U$1.P$5 (GND2), U$1.P$23 (GND3), U$1.P$49 (GND4), U$1.P$50 (GND5), U$1.P$51 (GND6), U$1.P$52 (GND7), U$1.P$99 (GND8), U$1.P$100 (GND9), U$2.GND1, U$2.GND2, US2.P5 (5), US2.P6 (6), US3_SONAR.P5 (5), US3_SONAR.P6 (6), US6.P5 (5), US6.P6 (6)
unnamed: SV4.2, U$2.DL (D_L)
unnamed: SV4.1, U$2.BL (B_L)
unnamed: Q1.C, R2.1, SJ1.3
unnamed: LED_PWR.A, R4.1
unnamed: LED1.K (C), R9.1
unnamed: IC3.2 (GND), R5.1, R6.1
unnamed: LED2.K (C), R10.1
unnamed: IC4.2 (GND), R7.2, R8.1
unnamed: I2C3_IMU.P5 (5), R11.2
unnamed: AN1.P1 (1), AN1.P2 (2), JP1.2
PA2/USART2_TX: U$1.P$14 (PA2), US2.P3 (3)
PA3/USART2_RX: U$1.P$13 (PA3), US2.P4 (4)
PA7/PWM: R9.2, U$1.P$17 (PA7)
PA8/I2C3_SCL: SV4.3, U$1.P$93 (PA8)
PB0/PWM: U$1.P$22 (PB0)
PB1/PWM: R10.2, U$1.P$21 (PB1)
PB3/SPI1_SCK: SPI1.P4 (4), U$1.P$78 (PB3)
PB4/SPI1_MISO: SPI1.P3 (3), U$1.P$75 (PB4)
PB5/SPI1_MOSI: SPI1.P2 (2), U$1.P$76 (PB5)
PB6/USART1_TX: IC1.4 (DI), JP2.1, U$1.P$73 (PB6)
PB7/USART1_RX: IC1.1 (RO), JP2.3 (1), U$1.P$74 (PB7)
PB8/I2C1_SCL: U$1.P$69 (PB8), U$2.CL (C_L)
PB9/I2C1_SDA: U$1.P$70 (PB9), U$2.AL (A_L)
PC6/USART6_TX: U$1.P$97 (PC6), US6.P3 (3)
PC7/USART6_RX: U$1.P$98 (PC7), US6.P4 (4)
PC9/I2C3_SDA: SV4.4, U$1.P$96 (PC9)
PC10/USART3_TX: U$1.P$87 (PC10), US3_SONAR.P3 (3)
PC11/USART3_RX: SJ1.2, U$1.P$88 (PC11)
PD3: IC1.2 (RE/), IC1.3 (DE), U$1.P$81 (PD3)
PE2: U$1.P$65 (PE2)
PE7: RECV.1, U$1.P$25 (PE7)
PE9/PWM: SV1.1, U$1.P$27 (PE9)
PE11/PWM: SV2.1, U$1.P$29 (PE11)
PE13/PWM: SV3.1, U$1.P$31 (PE13)
PE14/PWM: U$1.P$32 (PE14)
SCL1: ESC.5, ESC.6, I2C1_ESC.P4 (4), U$2.CH (C_H)
SCL2: I2C3_IMU.P4 (4), R3.1, SV4.5, U$2.BH (B_H)
SDA1: ESC.3, ESC.4, I2C1_ESC.P3 (3), U$2.AH (A_H)
SDA2: I2C3_IMU.P3 (3), R1.1, SV4.6, U$2.DH (D_H)
SONAR_RX: Q1.B, SJ1.1, US3_SONAR.P4 (4)
SRVO1_PWR: IC4.3 (VO), R7.1, SRVO1.2
SRVO2_PWR: IC3.3 (VO), R5.2, SRVO2.2
VCC: C2.1, IC2.IN, IC3.1 (VI), IC4.1 (VI), J1.PWR, SJ3.1, SJ3.2

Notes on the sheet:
IMU & ESC
SERVO
* Conversor eh necessario?
* JPI permite escolher se vai se fazer uso do conversor com pull-ups.
* R1 e R3 nao estao montados por default.
POWER
* SJ3 pode ser soldado caso IC2 nao esteja montado e 5V regulados sejam fornecidos. * IC2 nao vem montado por default. * IC3 e IC4 nao vem montados por default.
* Para os servos RX24f, montar IC1. * Para servos Dongbu, remover IC1, e bypassar linhas de TX e RX atraves de JP2-1 e JP2-2.
* Para sonar XL-MaxSonar-EZ MB1200, soldar SJ1 na posiçao 2-3. * Para usar como linha de serial comum, soldar SJ1 na posiçao 1-2.
SONAR
SONAR & Perifericos
Layers (p/ silk e top/bottom) - 1, 16 17, 18, 20, 21, 22, 25, 26, 48, 49, 51, 52
R11 apenas para 'pular' uma trilha no esquematico.

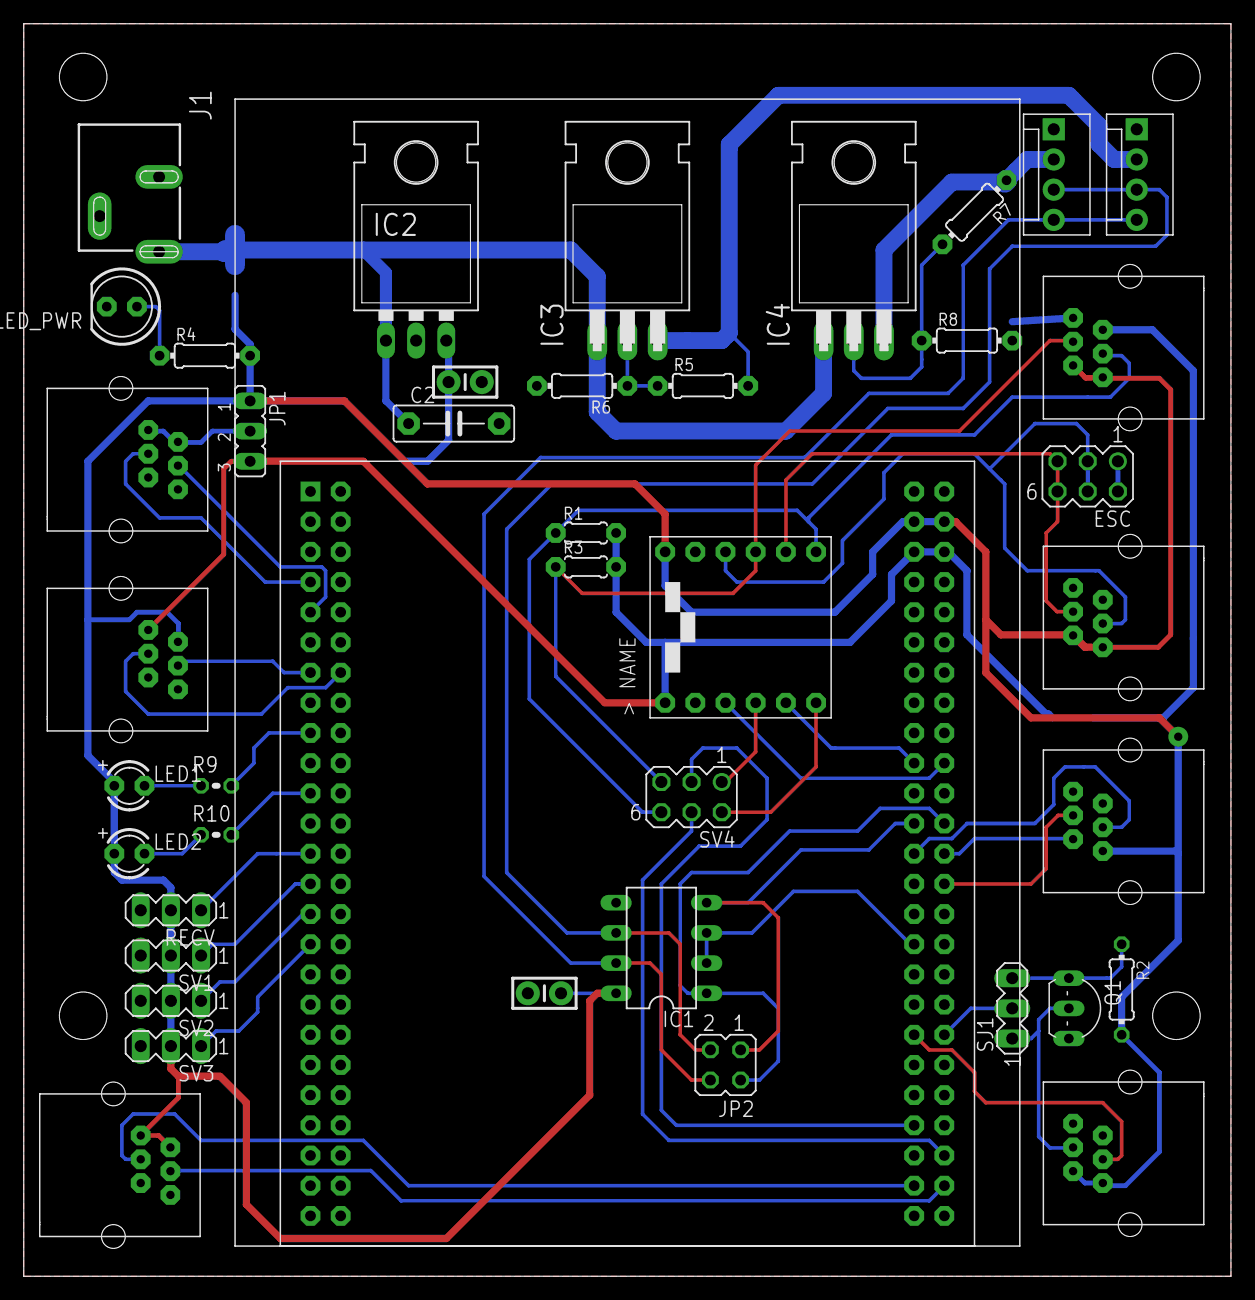
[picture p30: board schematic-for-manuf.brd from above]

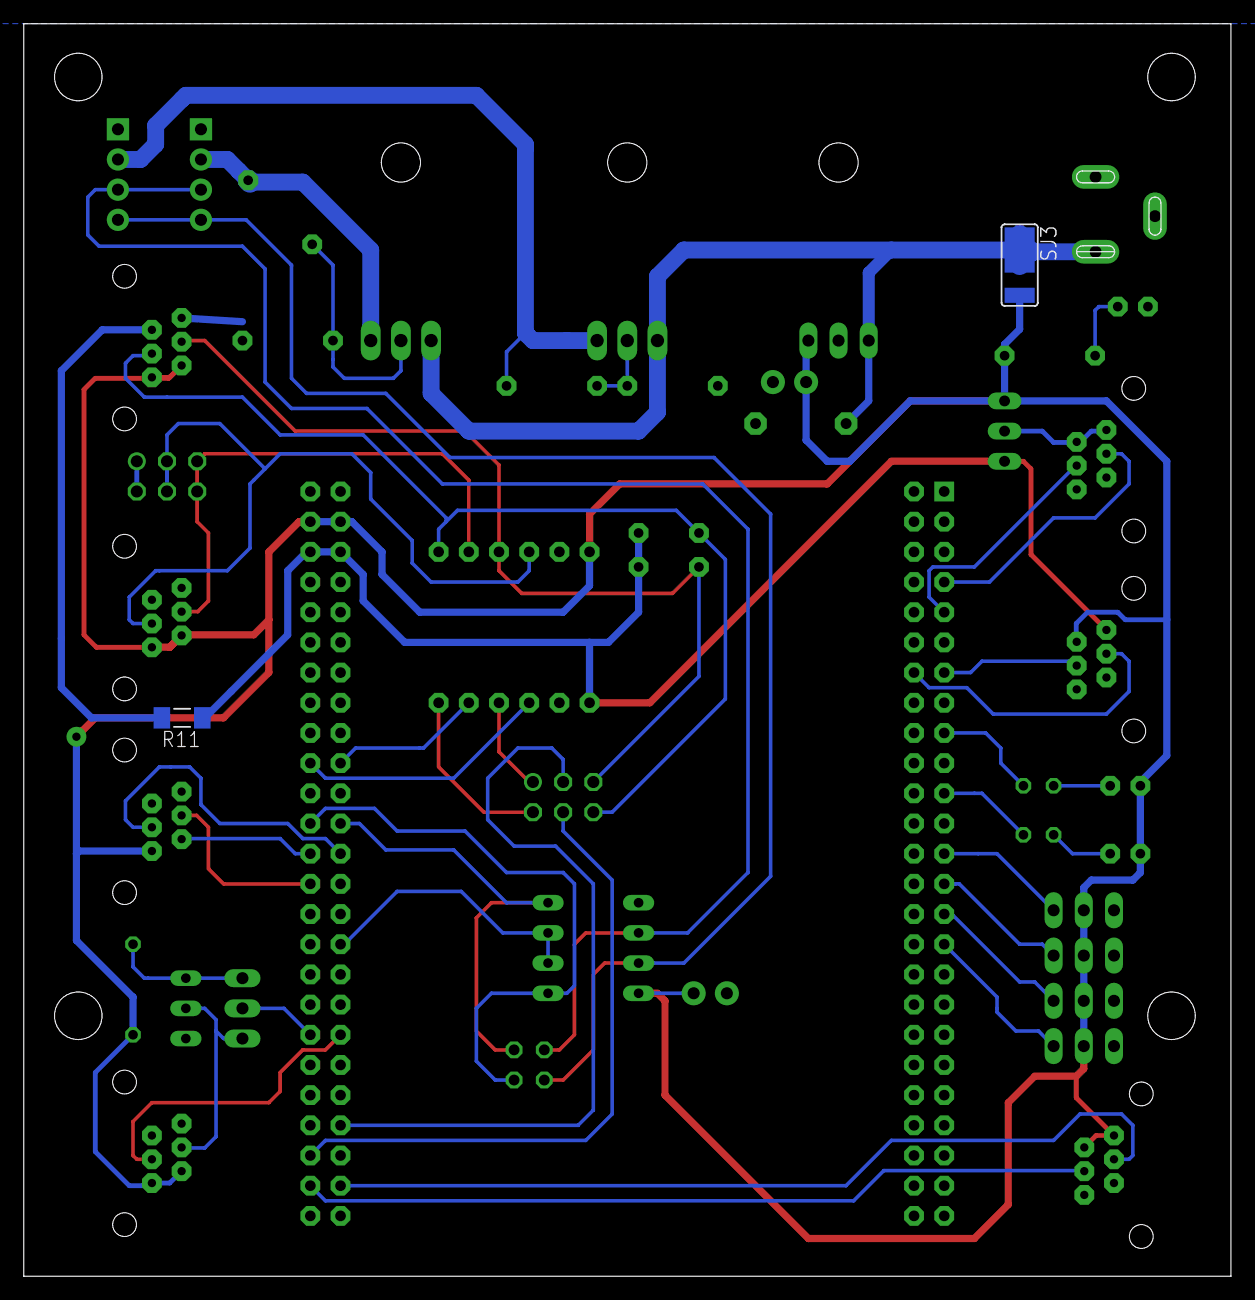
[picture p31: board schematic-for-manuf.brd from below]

Board: 2 copper layers, 101.6 x 105.4 mm, 44 parts (2 on the bottom side), 47 nets.

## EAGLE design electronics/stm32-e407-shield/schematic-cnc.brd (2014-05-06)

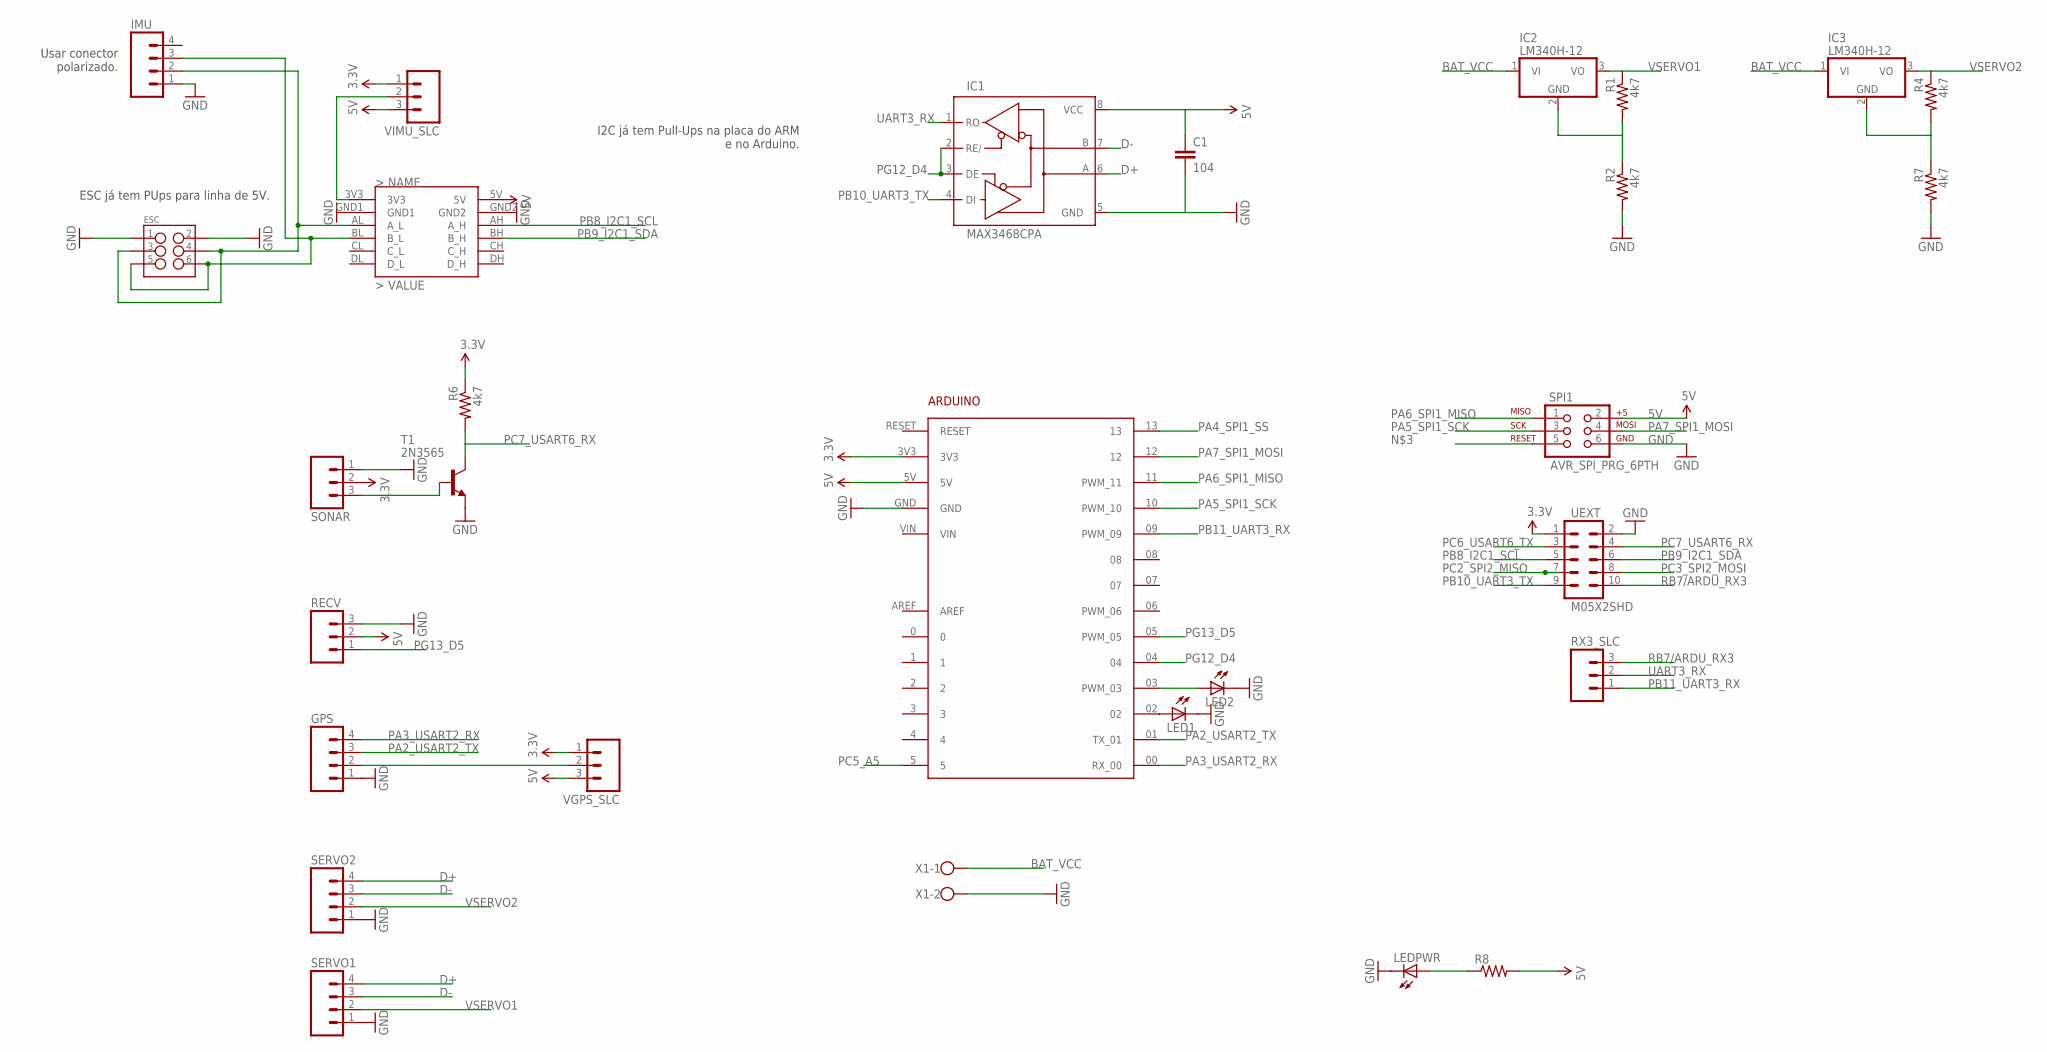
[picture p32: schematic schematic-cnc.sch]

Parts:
ARDUINO1: ARDUINO
C1: 104; CAP-PTH-SMALL-KIT
ESC: M03X22X3_SILK_SM; 2X3
GPS: M04PTH; 1X04
IC1: MAX3468CPA; DIL08
IC2, IC3: LM340H-12; TO220H
IMU: M04PTH; 1X04
LED1, LED2: LED3MM
LEDPWR: LED3MM
R1, R4: 4k7; 0309V
R2, R6, R7: 4k7; 0204/7
R8: RESISTORPTH-1/6W; 1/6W-RES
RECV: M03PTH; 1X03
RX3_SLC: M03PTH; 1X03
SERVO1, SERVO2: M04PTH; 1X04
SONAR: M03PTH; 1X03
SPI1: AVR_SPI_PRG_6PTH; 2X3
T1: 2N3565; TO92
U$1: JYMCU_LOGIC_LEVEL_CONVERTER; JYMCU_LOGIC_LEVEL_SHIFTER_DIP
UEXT: M05X2SHD; 2X5-SHROUDED
VGPS_SLC: M03PTH; 1X03
VIMU_SLC: M03PTH; 1X03
X1: W237-102

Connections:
3.3V: ARDUINO1.3V3, R6.1, SONAR.2, UEXT.1, VGPS_SLC.1, VIMU_SLC.1
5V: ARDUINO1.5V, C1.1, IC1.8 (VCC), R8.2, RECV.2, SPI1.2, U$1.5V, VGPS_SLC.3, VIMU_SLC.3
BAT_VCC: IC2.1 (VI), IC3.1 (VI), X1.1
D+: IC1.6 (A), SERVO1.4, SERVO2.4
D-: IC1.7 (B), SERVO1.3, SERVO2.3
GND: ARDUINO1.GND, C1.2, ESC.1, ESC.2, GPS.1, IC1.5 (GND), IMU.1, LED1.K (C), LED2.K (C), LEDPWR.K (C), R2.2, R7.2, RECV.3, SERVO1.1, SERVO2.1, SONAR.1, SPI1.6, T1.3 (E), U$1.GND1, U$1.GND2, UEXT.2, X1.2
unnamed: U$1.3V3, VIMU_SLC.2
unnamed: SONAR.3, T1.2 (B)
unnamed: ESC.3, ESC.4, IMU.2, U$1.AL (A_L)
unnamed: GPS.2, VGPS_SLC.2
unnamed: ARDUINO1.02, LED1.A
unnamed: ARDUINO1.03 (PWM_03), LED2.A
unnamed: LEDPWR.A, R8.1
unnamed: ESC.5, ESC.6, IMU.3, U$1.BL (B_L)
unnamed: IC3.2 (GND), R4.2, R7.1
unnamed: IC2.2 (GND), R1.2, R2.1
PA2_USART2_TX: ARDUINO1.01 (TX_01), GPS.3
PA3_USART2_RX: ARDUINO1.00 (RX_00), GPS.4
PA4_SPI1_SS: ARDUINO1.13
PA5_SPI1_SCK: ARDUINO1.10 (PWM_10), SPI1.3
PA6_SPI1_MISO: ARDUINO1.11 (PWM_11), SPI1.1
PA7_SPI1_MOSI: ARDUINO1.12, SPI1.4
PB8_I2C1_SCL: U$1.AH (A_H), UEXT.5
PB9_I2C1_SDA: U$1.BH (B_H), UEXT.6
PB10_UART3_TX: IC1.4 (DI), UEXT.9
PB11_UART3_RX: ARDUINO1.09 (PWM_09), RX3_SLC.1
PC2_SPI2_MISO: UEXT.7
PC3_SPI2_MOSI: UEXT.8
PC5_A5: ARDUINO1.5
PC6_USART6_TX: UEXT.3
PC7_USART6_RX: R6.2, T1.1 (C), UEXT.4
PG12_D4: ARDUINO1.04, IC1.2 (RE/), IC1.3 (DE)
PG13_D5: ARDUINO1.05 (PWM_05), RECV.1
RB7/ARDU_RX3: RX3_SLC.3, UEXT.10
UART3_RX: IC1.1 (RO), RX3_SLC.2
VSERVO1: IC2.3 (VO), R1.1, SERVO1.2
VSERVO2: IC3.3 (VO), R4.1, SERVO2.2

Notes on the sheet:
I2C já tem Pull-Ups na placa do ARM e no Arduino.
ESC já tem PUps para linha de 5V.
Usar conector polarizado.

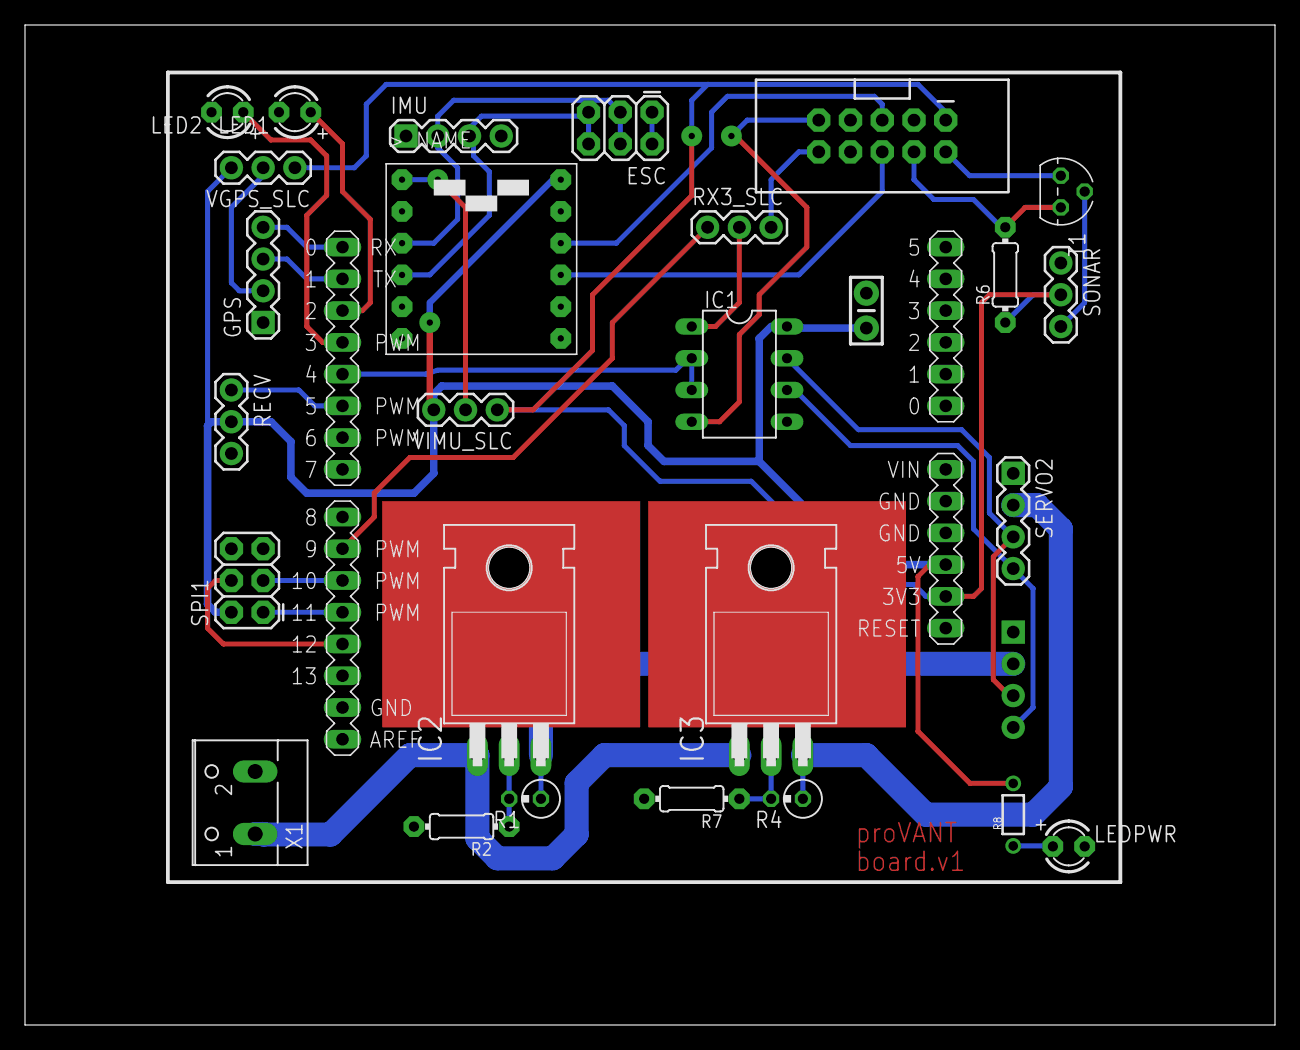
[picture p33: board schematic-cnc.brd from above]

Board: 2 copper layers, 100.0 x 80.0 mm, 29 parts (1 on the bottom side), 32 nets.

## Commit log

2014-01-22 Adição dos primeiros arquivos.
    Colocados arquivos base do repositório de mecânica e eletrônica.
    As versões ainda não são finais ou estáveis - um tag será liberado
    na primeira versão funcional dos arquivos.
    [3-5mm Bullit Plug.sldasm, 5v5a_converter.SLDPRT, 9v_45a_converter.SLDPRT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]
2014-01-29 Alterações no Shield para ARM e biblioteca padrão.
    O conversor lógico foi modelado no Eagle e adicionado à recem criada
    biblioteca provant_custom.lbr. Ele foi então usado para substituir
    o coversor lógico hard-core que havia sido previamente projetado.
    Planos para remover o IMU_SLC - ele agora influencia a tensão do
    barramento do ESC, o que não é desejado.
    new file: .gitignore
    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
    [schematic.brd, schematic.sch]
2014-02-04 Versão dual layer pra fabricação manual.
    [schematic.brd, schematic.sch]
2014-02-04 Criados os arquivos para fresa.
    Adicionados um layout e esquemático para fabricação dual layer em fresa.
    Trilhas foram espaçadas algumas foram passadas de bottom para top.
    R6 passou a ser through-hole. Pinos de terra foram identificados com
    uma anotação 'GND' no layer 48 (Document) uma vez que fresa não consegue
    trabalhar diretamente com o groud plane gerado pelo Eagle.
    new file: stm32-e407-shield/schematic-cnc.brd
    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
    [schematic-cnc.brd, schematic-cnc.sch]
2014-02-13 Pequenas correções depois da primeira tentativa de fabricação.
    [schematic.brd, schematic.sch]
2014-02-24 Inicio do projeto do Shield para STM32F4-Discovery.
2014-02-24 Adicionando arquivos do novo shield.
    [schematic.brd, schematic.sch]
2014-02-25 Iniciando o routing.
    [schematic.brd, schematic.sch]
2014-02-27 Primeira versao para fabricacao da placa STM32 Discovery.
    [schematic.brd, schematic.sch]
2014-03-01 Adicionadas algumas correcoes.
    [schematic.brd, schematic.sch]
2014-03-11 Alterados os pads do componente da STM32F4-Discovery (pads octogonais, 0.066 com o menor drill). Conectores alterados para serem compatíveis com plugs RJ11 (usando principalmente as 4 vias do centro).
    [schematic.brd, schematic.sch]
2014-03-11 Iniciando revisao da shield Discovery.
    [schematic.brd, schematic.sch]
2014-03-17 Alterado o layout da placa, removidas algumas frescuras.
    [schematic.brd, schematic.sch]
2014-03-20 Adicionado o jack para sensores analógicos. LEDs trocados para LEDs de 3mm. Verificaçao de routing do GND feita - aparentemente, sem problemas.
    [schematic.brd, schematic.sch]
2014-03-29 Realizado o roteamento Dual-Layer para fresamento.
    Aumento de espacamento (trilhas de 24mil, espacamento 24mil)
    [schematic.brd, schematic.sch]
2014-03-31 Small fixes.
    [schematic.brd, schematic.sch]
2014-05-04 Corrigido o conversor logico invertido e a pinagem incorreta de algumas portas.
    [schematic.brd, schematic.sch]
2014-05-23 modified: electronics/stm32f4discovery-shield/schematic.brd
    [schematic.brd]
2014-05-23 Mounting holes na placa.
    [schematic.brd]
2014-07-23 Correcoes finais a placa.
    - Conectores RECV, SV1, SV2 e SV3 movidos mais para a borda da placa.
    - 5V disponiveis no pino 2 do conector US6.
    - Conector US5_SONAR renomeado para US3_SONAR (por usar a USART3)
    - No conector I2C3_IMU, GND disponivel agora no pino 2 e 3v3 no pino 1.
    - Pino de GND do MAX485 ok (antes desconectado da malha de terra).
    - GND disponivel nos pinos 5 e 6 do conector US3_SONAR.
    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
    [schematic.brd, schematic.sch]
2014-08-14 Adicao dos sch/brd para o pedido de fabricacao.
    Esses arquivos deverao ser editados para atenderem as requiscoes do fabricante (toleracias, tamanhos) e serao utilzados para gerar os Gerbers de fabricacao.
    new file: schematic-for-manuf.brd
    new file: schematic-for-manuf.sch
    [schematic-for-manuf.brd, schematic-for-manuf.sch]
2014-08-18 Algumas alteracoes, adicao de anotacoes.
    [schematic-for-manuf.brd, schematic-for-manuf.sch]
2014-09-06 new file: .gitignore modified: electronics/stm32f4discovery-shield/anotacoes_para_manufatura.txt modified: electronics/stm32f4discovery-shield/schematic-for-manuf.brd
    [schematic-for-manuf.brd]
2014-09-09 Routing principal completo.
    [schematic-for-manuf.brd]
2014-09-12 Introduzido jumper para servo Dongbu.
    [schematic-for-manuf.brd, schematic-for-manuf.sch]
2014-09-15 Adicionados gerbers de fabricacao.
    - Adicionados configuracao de CAM para o Eagle
    - Adicionado tutorial de geracao de Gerbers
    - Imagens renderizadas da placa (a partir dos gerbers)
    [schematic-for-manuf.brd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]
2014-09-16 Atualizando tamanho do drill do logic-shifter.
    [schematic-for-manuf.brd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]
2014-09-16 Correcao dos gerbers (Windows gerou o silk errado, no Mac ficou OK)
    [provant_bottomcopper.GBL, provant_bottomsilk.GBO, provant_bottomsolder.GBS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]
2014-09-16 Adicionando printscreens da renderizacao dos novos gerbers.
2014-10-14 Adicionando manual de uso do shield.
2015-01-21 adicionado conectores para o gps
    [connector.brd, connector.sch]
2015-01-22 adicionado nota do numero 1 na placa para facilitar montagem
    [connector.brd]
2015-07-22 atualizando computador
    [connector.brd, connector.dxf]
2015-10-20 adicionando readme do GPS assim como a documentacao da placa para fazer a adaptacao das mensagens do GPS->VANT
    [arduino-mini-adapter.brd, arduino-mini-adapter.sch]
2015-10-20 modificando readme para para corringir problemas de interpretacao do github
2015-10-20 arrumando erros de portugues

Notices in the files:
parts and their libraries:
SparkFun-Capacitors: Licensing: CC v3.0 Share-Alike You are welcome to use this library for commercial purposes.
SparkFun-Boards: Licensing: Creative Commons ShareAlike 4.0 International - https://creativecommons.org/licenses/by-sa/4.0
